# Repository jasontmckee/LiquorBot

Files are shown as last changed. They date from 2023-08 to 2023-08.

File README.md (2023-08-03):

# LiquorBot

# Parts

## Printing
Parts are named using Voron-style conventions with [a] prefixes to denote accent color parts and quantity needed at the suffix. You'll need all parts from the main STLs directory plus the pump labels & octopus board mount from the single_color _or_ multi_color directories.

There are two options for the dispenser & drip tray. The basic version is what it says on the tin, a mount arm to attach the hoses to the leg and a simple tray to catch the drips. The led_sensor versions have provisions for a ring of 16 LEDs in the dispenser and a cup sensor switch in the drip tray (to prevent pouring a drink without a cup present).

All parts were printed at 0.20 layer height, 15% infill except for the pump pieces (see Pumps section below)

## Top plate and shelf
It's possible to make the top plate and shelf by hand using brackets as templates but it's _tedious_, I've done it a couple times on the different iterations of LiquorBot. That's why I've updated the CAD design from just laying out the parts and holes on the board to a set of SVGs suitable to be cut with a CNC.

Holes for the shelf and top plate leg brackets can be optionally counter-sunk for a smoother surface (hardware list assumes counter sunk screws for the shelf).

Holes for mounting the Raspberry Pi & screen will need to be hand-drilled.

## Hardware and parts

| Item | Qty | Location |
|---|-----|---|
| M3 nut | 18  | Pump bracket & power plug |
| M3S nut | 10  | Leg, dispenser & cup brackets |
| M3-8 countersunk | 20  | Plate/shelf to leg brackets |
| M3-16 | 16  | Pump bracket |
| M3-12 | 10  | Leg, dispenser & cup brackets |
| M3 heat insert | 4 | Controller board mount |
| M4-12 countersunk	 | 6 | Pump tags/hose clips |
| M4-16 countersunk	 | 2 | Controller board mount/hose clips |
| M2-8 countersunk | 2 | Cup sensor & LED dispenser head |
| M2x4x3.5 heat insert | 2 | Cup sensor & LED dispenser head |
| M2-10 self-tapping | 4 | Cup sensor switches |
| M4 washers | 48  | Pump rotors |
| M4 nuts | 56  | Pump rotors & housing |
| M4x20 | 24  | Pump rotors |
| M4x25 | 32  | Pump housing |

| Item | Qty | Source |
|---|-----|---|
| 18"/460mm 3/4"/19mm aluminum tubing | 4 |  |
| 5"/130mm 3/4"/19mm aluminum tubing | 2 |  |
| furniture leg caps | 6 | https://amazon.com/uxcell-Furniture-Protector-Prevent-Scratches/dp/B07PGS84Y6 |
| micro switches | 2 | https://www.amazon.com/gp/product/B07FJ77HNV |
| Big Tree Tech Octopus board | 1 | https://biqu.equipment/products/bigtreetech-octopus-v1-1?variant=39749194023010 |
| 16 LED neopixel ring light | 1 | https://amazon.com/dp/B0B2D5QXG5 |
| 3 & 4 pin JST connectors | 1ea | https://aliexpress.us/item/2251832574216984.html	|
| 2.5mm power socket | 1 | https://www.amazon.com/gp/product/B078YNW3JZ |
| 24V power supply | 1 | https://amazon.com/gp/product/B01GC6VS8I |
| Nema17 Stepper motors, 24mm shaft | 8 | https://www.amazon.com/dp/B088B756MY/?coliid=I3CAV1IQ1ES0T8 |
| 13x4x5 (ODBoreW) bearings for pump rotor | 48  | https://www.amazon.com/dp/B094D6C3ZN |
| 6x4mm silicone tubing | 16m | https://www.amazon.com/dp/B08PTXZ51Q |

Raspberry pi + touchscreen and case, I used https://smarticase.com/collections/all-products/products/smartipi-touch-2

Tubing lengths can be adjusted for shorter/taller bottles

## Pumps
You'll also need to print & build 8 sets of pumps and 2 brackets from Ryan Dibisch's excellent nema17-based peristalic pump model: https://www.thingiverse.com/thing:1134817 There is some variability of inner diameter and squishiness of silicone hoses, so you may need to print thicker or thinner pressure plates from the pump_mods folder. Plates are labeled as how many millimeters thicker or thinner the space for the hose is relative to the stock design.

# Assembly

TODO: pictures are worth 1000 words

# Configure
LiquorBot is effectively a 3d printer that extrudes drink ingredients and configuration is the same as any other [Klipper](https://www.klipper3d.org/)-based 3d printer. [KIAUH](https://github.com/th33xitus/kiauh) is an easy path to get Klipper installed and running. Follow Big Tree Tech's [instructions](https://github.com/bigtreetech/BIGTREETECH-OCTOPUS-V1.0/tree/master/Firmware/Klipper) for installing klipper firmware on the Octopus board and connecting it to the pi.

Once Klipper is installed, be sure to change the `serial` parameter in [printer.cfg](config/printer.cfg) to match your board (see BTT instructions above).

# Tuning
Using the PUMP macro with a relatively low SPEED parameter (about 100) for each pump, start with a relatively loose pressure plate and switch to increasingly tighter ones until you find one that will both pump water and not leak/siphon/drip when the pump is off. Once you have the rigth pressure plate, test with increasing SPEED parameters until you find the fastest speed that will reliably run without stalling the stepper. On my machine, most pumps run at about 250, but some need to be backed off to 210. Set the default speed for each pump in the DISPENSE_NO_CHECK macro.

The PUMP macro is also where volumetric units are converted into mm of rotation. You'll want to adjust the multiplier in the MANUAL_STEPPER MOVE parameter so that the volume dispensed matches the volume requested. My machine needs 1862mm for 1oz or 63mm per milliliter.

# API
Moonraker provides a HTTP interface to run gcode, see "Run a gcode" on https://moonraker.readthedocs.io/en/latest/web_api/ for details. 

LiquorBot's main API macros are:
 * DISPENSE - takes a volume for each pump (p1 through p8), waits until the cup sensor reports a cup present and then calls DISPENSE_NO_CHECK
 * DISPENSE_NO_CHECK - takes same parameters as DISPENSE but doens't check if a cup is present before calling PUMP macro for each pump. Use this if you're not using the cup sensor. SPEED parameter can be used to override the default speed for all pumps
 * PRIME - pumps slightly more than the volume contained in the tubing for each pump. Call this when connecting all bottle for the first time
 * UNLOAD - opposite of PRIME, reverses the pumps to put any product still in the hoses back into the bottles
 * CLEAN - runs several oz through each pump, useful to flush the hoses with water and/or vodka for cleaning

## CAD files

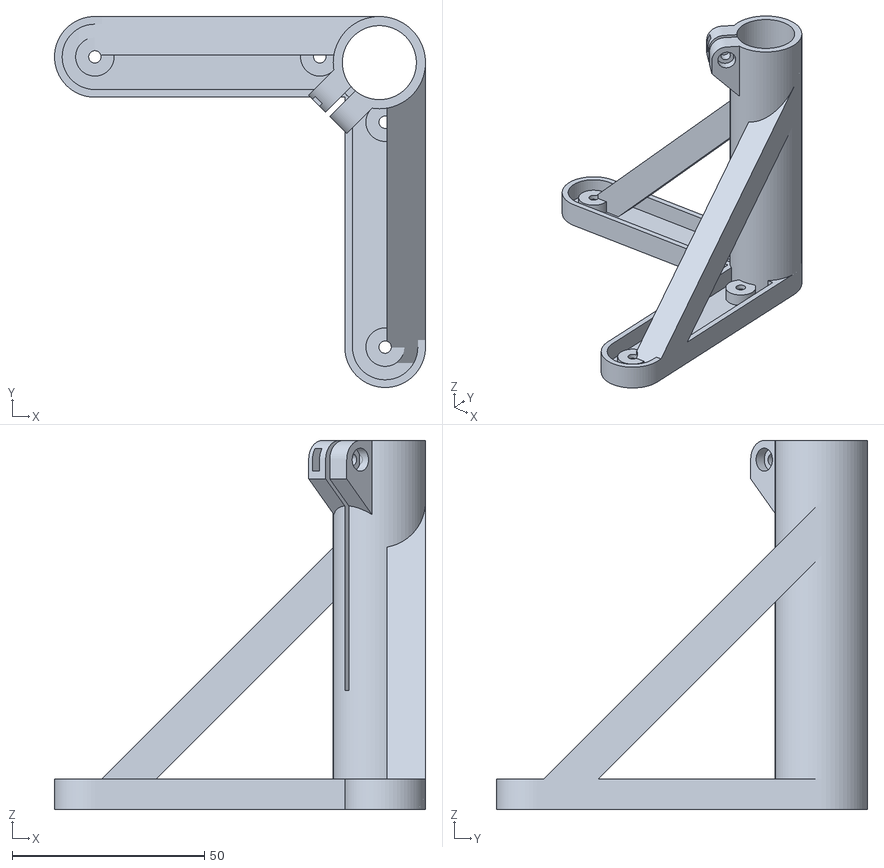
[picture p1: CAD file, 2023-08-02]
STLs/main_plate_bracket_x4.stl
96.5 x 96.5 x 96.0

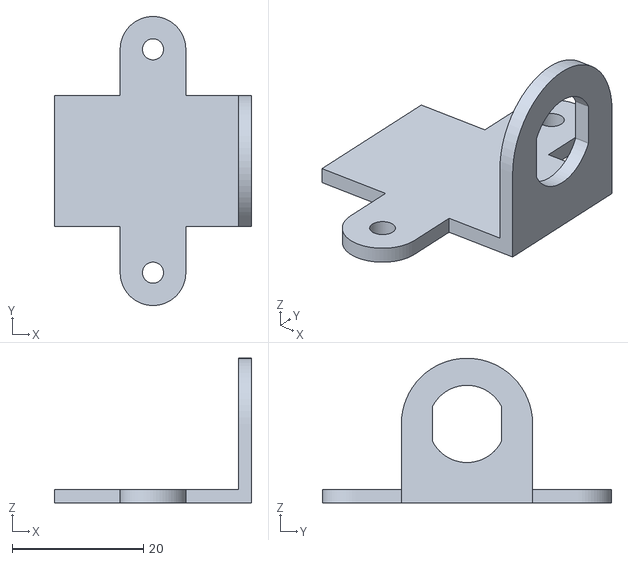
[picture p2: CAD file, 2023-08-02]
STLs/[a]_power_socket_lower_x1.stl
30.0 x 44.0 x 22.0

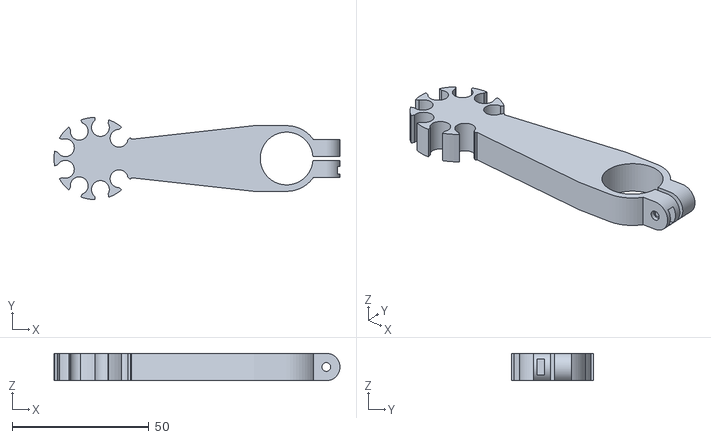
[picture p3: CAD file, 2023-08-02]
STLs/basic/basic_dispenser_x1.stl
104.5 x 30.0 x 10.0

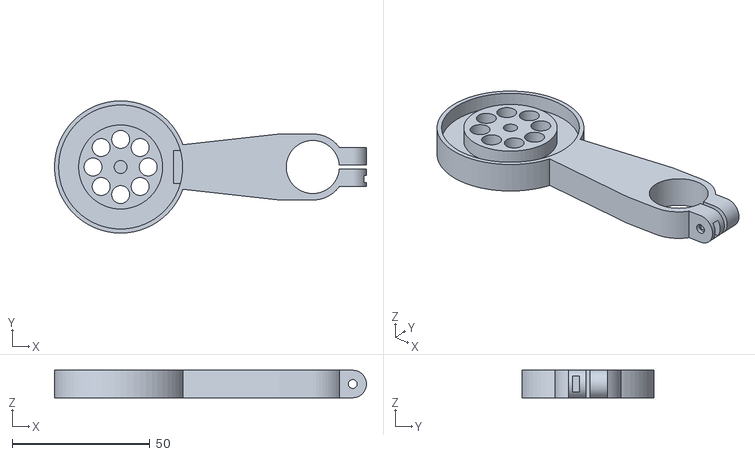
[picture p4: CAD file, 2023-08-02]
STLs/led_sensor/led_dispenser_x1.stl
113.2 x 48.0 x 10.0

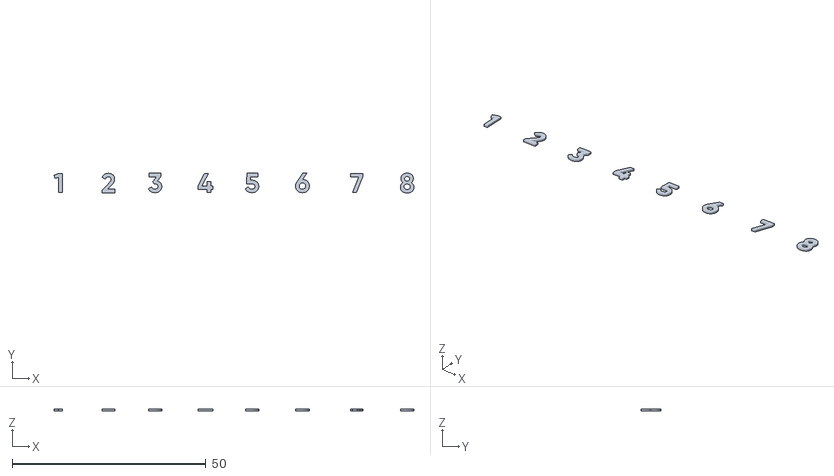
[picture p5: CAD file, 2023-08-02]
STLs/multi_color/[a]_two_color_pump_tags_labels_x1.stl
92.8 x 5.14 x 0.5

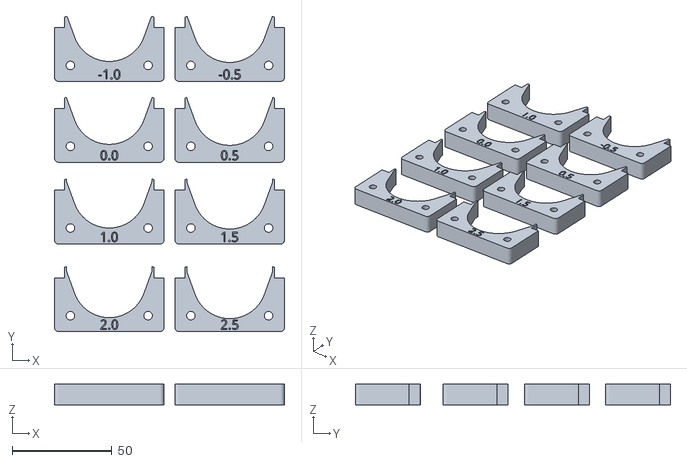
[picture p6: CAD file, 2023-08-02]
STLs/pump_mods/hose_pressure_plates.stl
115.5 x 158.3 x 10.5

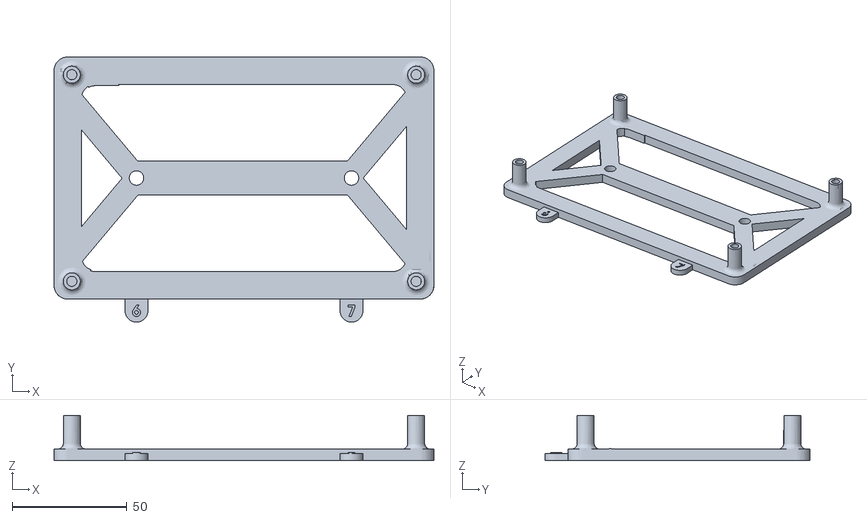
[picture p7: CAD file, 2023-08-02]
STLs/single_color/one_color_octopus_mount_x1.stl
165.5 x 115.5 x 19.7

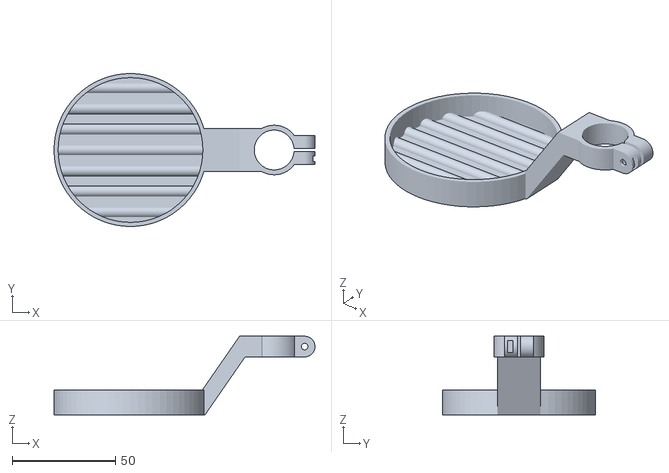
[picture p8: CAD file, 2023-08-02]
STLs/basic/basic_drip_tray_x1.stl
126.2 x 74.0 x 38.0

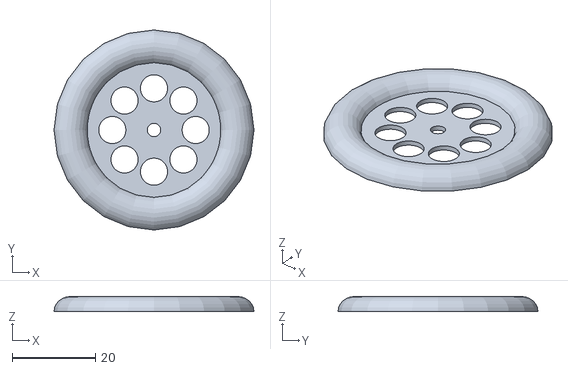
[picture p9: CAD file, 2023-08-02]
STLs/led_sensor/led_dispenser_clear_lens_x1.stl
48.0 x 48.0 x 3.60

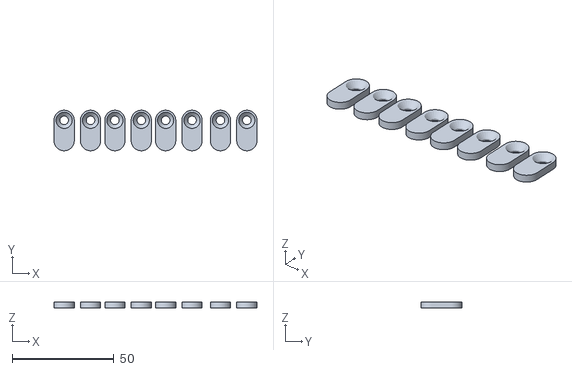
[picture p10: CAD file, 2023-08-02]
STLs/multi_color/two_color_pump_tags_x1.stl
100.0 x 20.0 x 3.00

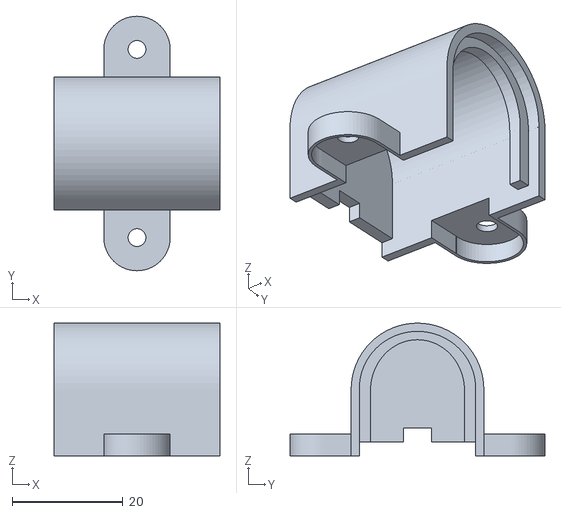
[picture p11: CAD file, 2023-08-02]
STLs/power_socket_upper_x1.stl
30.0 x 46.0 x 24.0

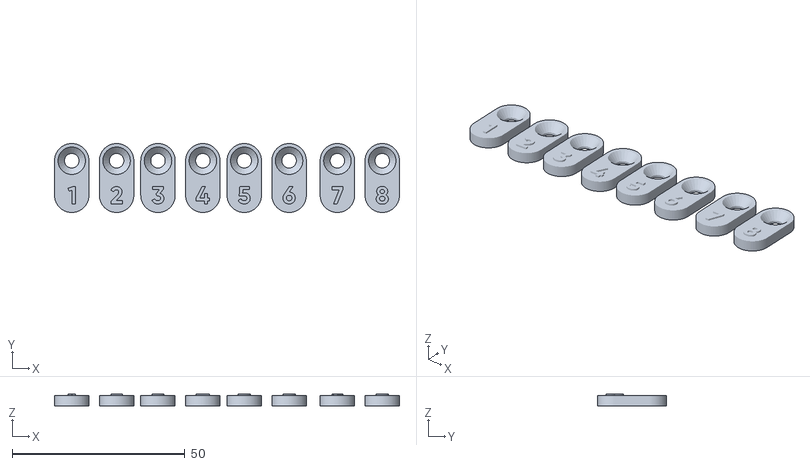
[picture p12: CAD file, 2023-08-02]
STLs/single_color/one_color_pump_tags_x1.stl
100.0 x 20.0 x 3.50

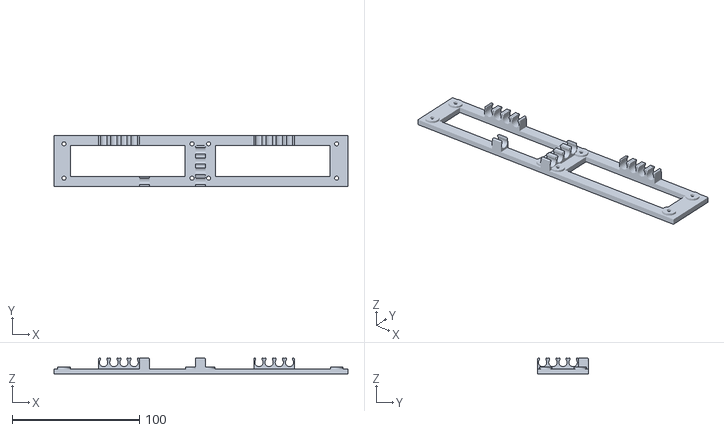
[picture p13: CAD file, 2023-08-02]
STLs/[a]_hose_pump_bracket_right_x1.stl
231.0 x 40.0 x 12.5

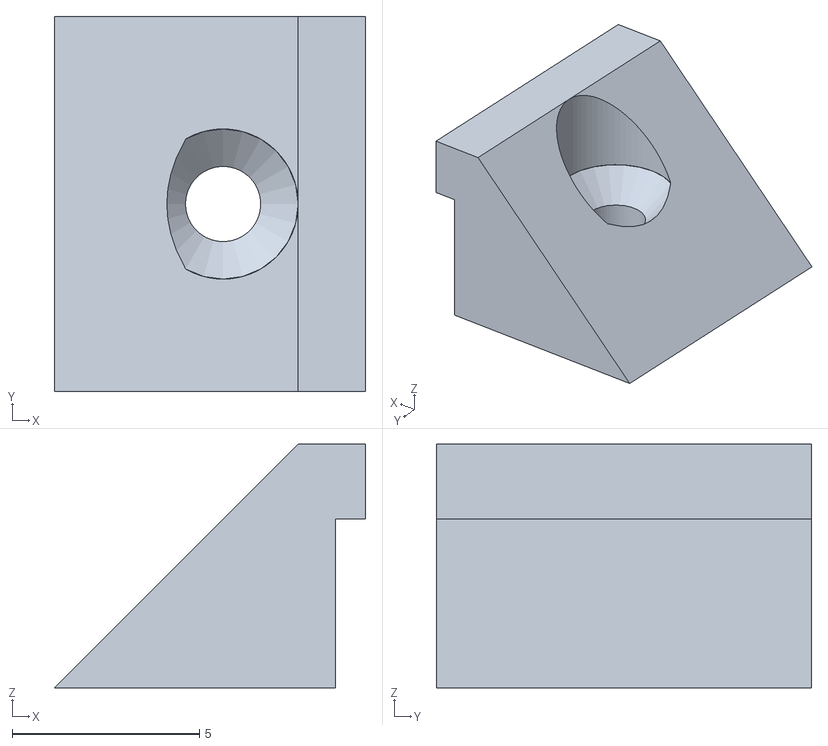
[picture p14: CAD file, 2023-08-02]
STLs/led_sensor/[a]_sensor_drip_tray_plug_retainer_x1.stl
8.30 x 10.0 x 6.50

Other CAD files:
STLs/multi_color/[a]_two_color_octopus_mount_labels_x1.stl
STLs/led_sensor/sensor_drip_tray_upper_x1.stl
STLs/lower_shelf_bracket_x2.stl
STLs/multi_color/two_color_octopus_mount_x1.stl
STLs/[a]_hose_bundle_bracket_x3.stl
STLs/[a]_hose_pump_bracket_left_x1.stl
STLs/[a]_plumbing_fixtures_x1.stl
STLs/dispenser_head_x1.stl
STLs/led_sensor/[a]_cable_clip_x2.stl
STLs/led_sensor/[a]_led_dispenser_plug_retainer.stl
STLs/led_sensor/sensor_drip_tray_lower_x1.stl

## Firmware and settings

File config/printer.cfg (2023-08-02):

[include mainsail.cfg]

[mcu]
serial: /dev/serial/by-id/usb-Klipper_stm32f446xx_REPLACE_WITH_YOUR_VALUE

[printer]
kinematics: none
max_velocity: 100
max_accel: 1000

#
# LED control
#
[neopixel rgb1]
pin: PB0
chain_count: 16
initial_RED: 0.5
initial_GREEN: 0.0
initial_BLUE: 0.0
#initial_WHITE: 0.0

#
# cup sensor
#
[gcode_button cup_sensor]
pin: PG6
press_gcode:
  SET_GCODE_VARIABLE MACRO=DISPENSE VARIABLE=cup_present VALUE=1
  SET_LED LED=rgb1 GREEN=0.5
release_gcode:
  SET_GCODE_VARIABLE MACRO=DISPENSE VARIABLE=cup_present VALUE=0
  SET_LED LED=rgb1 BLUE=0.5

# Driver0
[manual_stepper pump1]
step_pin: PF13
dir_pin: PF12
enable_pin: !PF14
microsteps: 16
rotation_distance: 40

# Driver1
[manual_stepper pump2]
step_pin: PG0
dir_pin: PG1
enable_pin: !PF15
microsteps: 16
rotation_distance: 40

# Driver2
[manual_stepper pump3]
step_pin: PF11
dir_pin: PG3
enable_pin: !PG5
microsteps: 16
rotation_distance: 40

# Driver3
[manual_stepper pump4]
step_pin: PG4
dir_pin: PC1
enable_pin: !PA0
microsteps: 16
rotation_distance: 40

# Driver4
[manual_stepper pump5]
step_pin: PF9
dir_pin: PF10
enable_pin: !PG2
microsteps: 16
rotation_distance: 40

# Driver5
[manual_stepper pump6]
step_pin: PC13
dir_pin: PF0
enable_pin: !PF1
microsteps: 16
rotation_distance: 40

# Driver6
[manual_stepper pump7]
step_pin: PE2
dir_pin: PE3
enable_pin: !PD4
microsteps: 16
rotation_distance: 40

# Driver7
[manual_stepper pump8]
step_pin: PE6
dir_pin: PA14
enable_pin: !PE0
microsteps: 16
rotation_distance: 40

########################################
# TMC2209 configuration
########################################

#
# SL42STH38-1684A rated at 1.65A, run_current can bump up to 1.16
#

[tmc2209 manual_stepper pump1]
uart_pin: PC4
run_current: 1.100
hold_current: 0.1
stealthchop_threshold: 999999

[tmc2209 manual_stepper pump2]
uart_pin: PD11
run_current: 1.100
hold_current: 0.1
stealthchop_threshold: 999999

[tmc2209 manual_stepper pump3]
uart_pin: PC6
run_current: 1.100
hold_current: 0.1
stealthchop_threshold: 999999

[tmc2209 manual_stepper pump4]
uart_pin: PC7
run_current: 1.100
hold_current: 0.1
stealthchop_threshold: 999999

[tmc2209 manual_stepper pump5]
uart_pin: PF2
run_current: 1.100
hold_current: 0.1
stealthchop_threshold: 999999

[tmc2209 manual_stepper pump6]
uart_pin: PE4
run_current: 1.100
hold_current: 0.1
stealthchop_threshold: 999999

[tmc2209 manual_stepper pump7]
uart_pin: PE1
run_current: 1.100
hold_current: 0.1
stealthchop_threshold: 999999

[tmc2209 manual_stepper pump8]
uart_pin: PD3
run_current: 1.100
hold_current: 0.1
stealthchop_threshold: 999999

#
# Macros
#

#
# main dispense entry point
# sets params and then uses wait_for_cup to ensure a cup is present
#
[gcode_macro DISPENSE]
variable_cup_present: 0
variable_p1: 0.0
variable_p2: 0.0
variable_p3: 0.0
variable_p4: 0.0
variable_p5: 0.0
variable_p6: 0.0
variable_p7: 0.0
variable_p8: 0.0
gcode:
  SET_GCODE_VARIABLE MACRO=DISPENSE VARIABLE=p1 VALUE={params.P1|default(0)|float}
  SET_GCODE_VARIABLE MACRO=DISPENSE VARIABLE=p2 VALUE={params.P2|default(0)|float}
  SET_GCODE_VARIABLE MACRO=DISPENSE VARIABLE=p3 VALUE={params.P3|default(0)|float}
  SET_GCODE_VARIABLE MACRO=DISPENSE VARIABLE=p4 VALUE={params.P4|default(0)|float}
  SET_GCODE_VARIABLE MACRO=DISPENSE VARIABLE=p5 VALUE={params.P5|default(0)|float}
  SET_GCODE_VARIABLE MACRO=DISPENSE VARIABLE=p6 VALUE={params.P6|default(0)|float}
  SET_GCODE_VARIABLE MACRO=DISPENSE VARIABLE=p7 VALUE={params.P7|default(0)|float}
  SET_GCODE_VARIABLE MACRO=DISPENSE VARIABLE=p8 VALUE={params.P8|default(0)|float}
  UPDATE_DELAYED_GCODE ID=wait_for_cup DURATION=0.1

#
# effectively polls until the cup present button is triggered, then calls DISPENSE_NO_CHECK to actually pour drinks
#
[delayed_gcode wait_for_cup]
gcode:
  {% if printer["gcode_macro DISPENSE"].cup_present==1 %}
  SET_LED LED=rgb1 BLUE=0.5 GREEN=0 RED=0
  DISPENSE_NO_CHECK P1={printer["gcode_macro DISPENSE"].p1} P2={printer["gcode_macro DISPENSE"].p2} P3={printer["gcode_macro DISPENSE"].p3} P4={printer["gcode_macro DISPENSE"].p4} P5={printer["gcode_macro DISPENSE"].p5} P6={printer["gcode_macro DISPENSE"].p6} P7={printer["gcode_macro DISPENSE"].p7} P8={printer["gcode_macro DISPENSE"].p8} 
  {% else %}
  SET_LED LED=rgb1 RED=0.5
  UPDATE_DELAYED_GCODE ID=wait_for_cup DURATION=0.5
  {% endif %}

#
# same API as DISPENSE but doesn't check for cup presence before pouring
#
[gcode_macro DISPENSE_NO_CHECK]
gcode:
  {% set p1 = params.P1|default(0)|float %}
  {% set p2 = params.P2|default(0)|float %}
  {% set p3 = params.P3|default(0)|float %}
  {% set p4 = params.P4|default(0)|float %}
  {% set p5 = params.P5|default(0)|float %}
  {% set p6 = params.P6|default(0)|float %}
  {% set p7 = params.P7|default(0)|float %}
  {% set p8 = params.P8|default(0)|float %}
  SET_LED LED=rgb1 RED=0 GREEN=0 BLUE=0

  SET_LED LED=rgb1 RED=1 GREEN=0. BLUE=0. INDEX=1
  SET_LED LED=rgb1 RED=1 GREEN=0.25 BLUE=0. INDEX=2
  PUMP PUMP=1 VOLUME={p1} SPEED={params.SPEED|default(240)|float}
  SET_LED LED=rgb1 RED=1 GREEN=0.5 BLUE=0. INDEX=3
  SET_LED LED=rgb1 RED=1 GREEN=0.75 BLUE=0. INDEX=4
  PUMP PUMP=2 VOLUME={p2} SPEED={params.SPEED|default(250)|float}
  SET_LED LED=rgb1 RED=1 GREEN=1 BLUE=0. INDEX=5
  SET_LED LED=rgb1 RED=0.75 GREEN=1 BLUE=0. INDEX=6
  PUMP PUMP=3 VOLUME={p3} SPEED={params.SPEED|default(230)|float}
  SET_LED LED=rgb1 RED=0.5 GREEN=1 BLUE=0. INDEX=7
  SET_LED LED=rgb1 RED=0.25 GREEN=1 BLUE=0. INDEX=8
  PUMP PUMP=4 VOLUME={p4} SPEED={params.SPEED|default(250)|float}
  SET_LED LED=rgb1 RED=0. GREEN=1 BLUE=0.25 INDEX=9
  SET_LED LED=rgb1 RED=0. GREEN=1 BLUE=0.5 INDEX=10
  PUMP PUMP=5 VOLUME={p5} SPEED={params.SPEED|default(250)|float}
  SET_LED LED=rgb1 RED=0. GREEN=1 BLUE=0.75 INDEX=11
  SET_LED LED=rgb1 RED=0. GREEN=0.75 BLUE=1 INDEX=12
  PUMP PUMP=6 VOLUME={p6} SPEED={params.SPEED|default(250)|float}
  SET_LED LED=rgb1 RED=0. GREEN=0.5 BLUE=1 INDEX=13
  SET_LED LED=rgb1 RED=0.25 GREEN=0. BLUE=1 INDEX=14
  PUMP PUMP=7 VOLUME={p7} SPEED={params.SPEED|default(210)|float}
  SET_LED LED=rgb1 RED=0.50 GREEN=0. BLUE=1 INDEX=15
  SET_LED LED=rgb1 RED=0.75 GREEN=0. BLUE=1 INDEX=16
  PUMP PUMP=8 VOLUME={p8} SPEED={params.SPEED|default(200)|float}
  SET_LED LED=rgb1 GREEN=0.5

#
# convienience method for maintenance
#
[gcode_macro PRIME]
gcode:
  DISPENSE_NO_CHECK P1=1 P2=1 P3=1 P4=1 P5=1 P6=1 P7=1 P8=1 SPEED=200

#
# convienience method for maintenance
#
# reverse speed seems to need to be slower for some reason
#
[gcode_macro UNLOAD]
gcode:
  DISPENSE_NO_CHECK P1=-1.5 P2=-1.5 P3=-1.5 P4=-1.5 P5=-1.5 P6=-1.5 P7=-1.5 P8=-1.5 SPEED=175

#
# convienience method for maintenance
#
[gcode_macro CLEAN]
gcode:
  DISPENSE_NO_CHECK P1=2 P2=2 P3=2 P4=2 P5=2 P6=2 P7=2 P8=2 

#
# translates oz to mm of stepper movement
#
[gcode_macro PUMP]
# 1862 "mm" per oz
# 63 "mm" per ml
gcode:
  MANUAL_STEPPER STEPPER=pump{params.PUMP} SET_POSITION=0 SPEED={params.SPEED|default(250)|float} MOVE={params.VOLUME|float * 1862} 
  

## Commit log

2023-08-02 initial import of LiquorBot mk5
    [[a]_cable_clip_x2.stl, [a]_hose_bundle_bracket_x3.stl, [a]_hose_pump_bracket_left_x1.stl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]
2023-08-03 added pump hardware
2023-08-03 added steppers, more links
2023-08-03 added drivers for octopus
2023-08-10 increased stroke width on SVGs to 0.01mm to render visually
